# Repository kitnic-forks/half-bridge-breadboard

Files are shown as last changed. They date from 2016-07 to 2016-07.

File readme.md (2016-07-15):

# Purpose #

This is a KiCad project that documents a simple half-bridge circuit, complete with driver.  The
circuit includes room for two TO-220 MOSFETs, two snubber circuits.  It has two logic-level inputs 
which will turn on the upper and lower MOSFETs.

# Details of Operation #

## Power Supply ##

If 10V < V<sub>BATT</sub> < 20V, then the jumper at P2 may be connected so that the
[FAN7842MX](https://www.fairchildsemi.com/datasheets/FA/FAN7842.pdf) is properly supplied.

If V<sub>BATT</sub> < 10V or V<sub>BATT</sub> > 20V, then the user must supply a voltage
between 10V and 20V to the circuit using pin 1 of P1.

## PWM Frequency ##

The circuit is intended to operate as a complete half-bridge using Pulse Width Modulation (PWM) on
the high side AND the low side.  When the upper MOSFET is being operated, it must be operated
synchronously with the lower MOSFET in order to charge the bootstrap capacitor.  The minimum recommended
PWM frequency is 10kHz.

When only the lower MOSFET is being operated, then the upper MOSFET input may be held low while the
lower MOSFET is operated at any frequency desired, including DC.

## Specifications ##

The circuit is intended to operate at a maximum voltage of ~35V and 5A, but these are limitations of
the components and not of the circuit board.  The board - with the proper capacitors and MOSFETs -
should be able to operate as high as 200V at a current of up to 20A.

## Connections ##

### Breadboard ###

If the breatboard power rails are between 10V and 20V and the expected current is under 1A, then P1,
P2, and P3 can be populated on the underside of the board and simply plugged into the breadboard.

When the voltage is outside of the 10V to 20V range, then only pins 1, 2, and 3 of P2 should be
populated and plugged into the breadboard.  The 10V-20V should be supplied to the board through
pin 1 of P1.

### Screw Terminals ###

If P2 is not populated, then power may be supplied through the screw terminals on P4.

# Why Do This? #

I know that there are lots of these sorts of circuits available, but I am continually finding myself
re-drawing this schematic for different circuits.  By placing all of the components for the half-bridge
on one circuit, I have a flexible and extendable starting point for a host of circuits.  Applications
include:

 * DC-DC conversion
 * DC motor drives
 * BLDC motor drives
 
I had a look around and didn't see anything quite like it on Tindie nor a couple of other sites that
I frequent.  World, here ya go.

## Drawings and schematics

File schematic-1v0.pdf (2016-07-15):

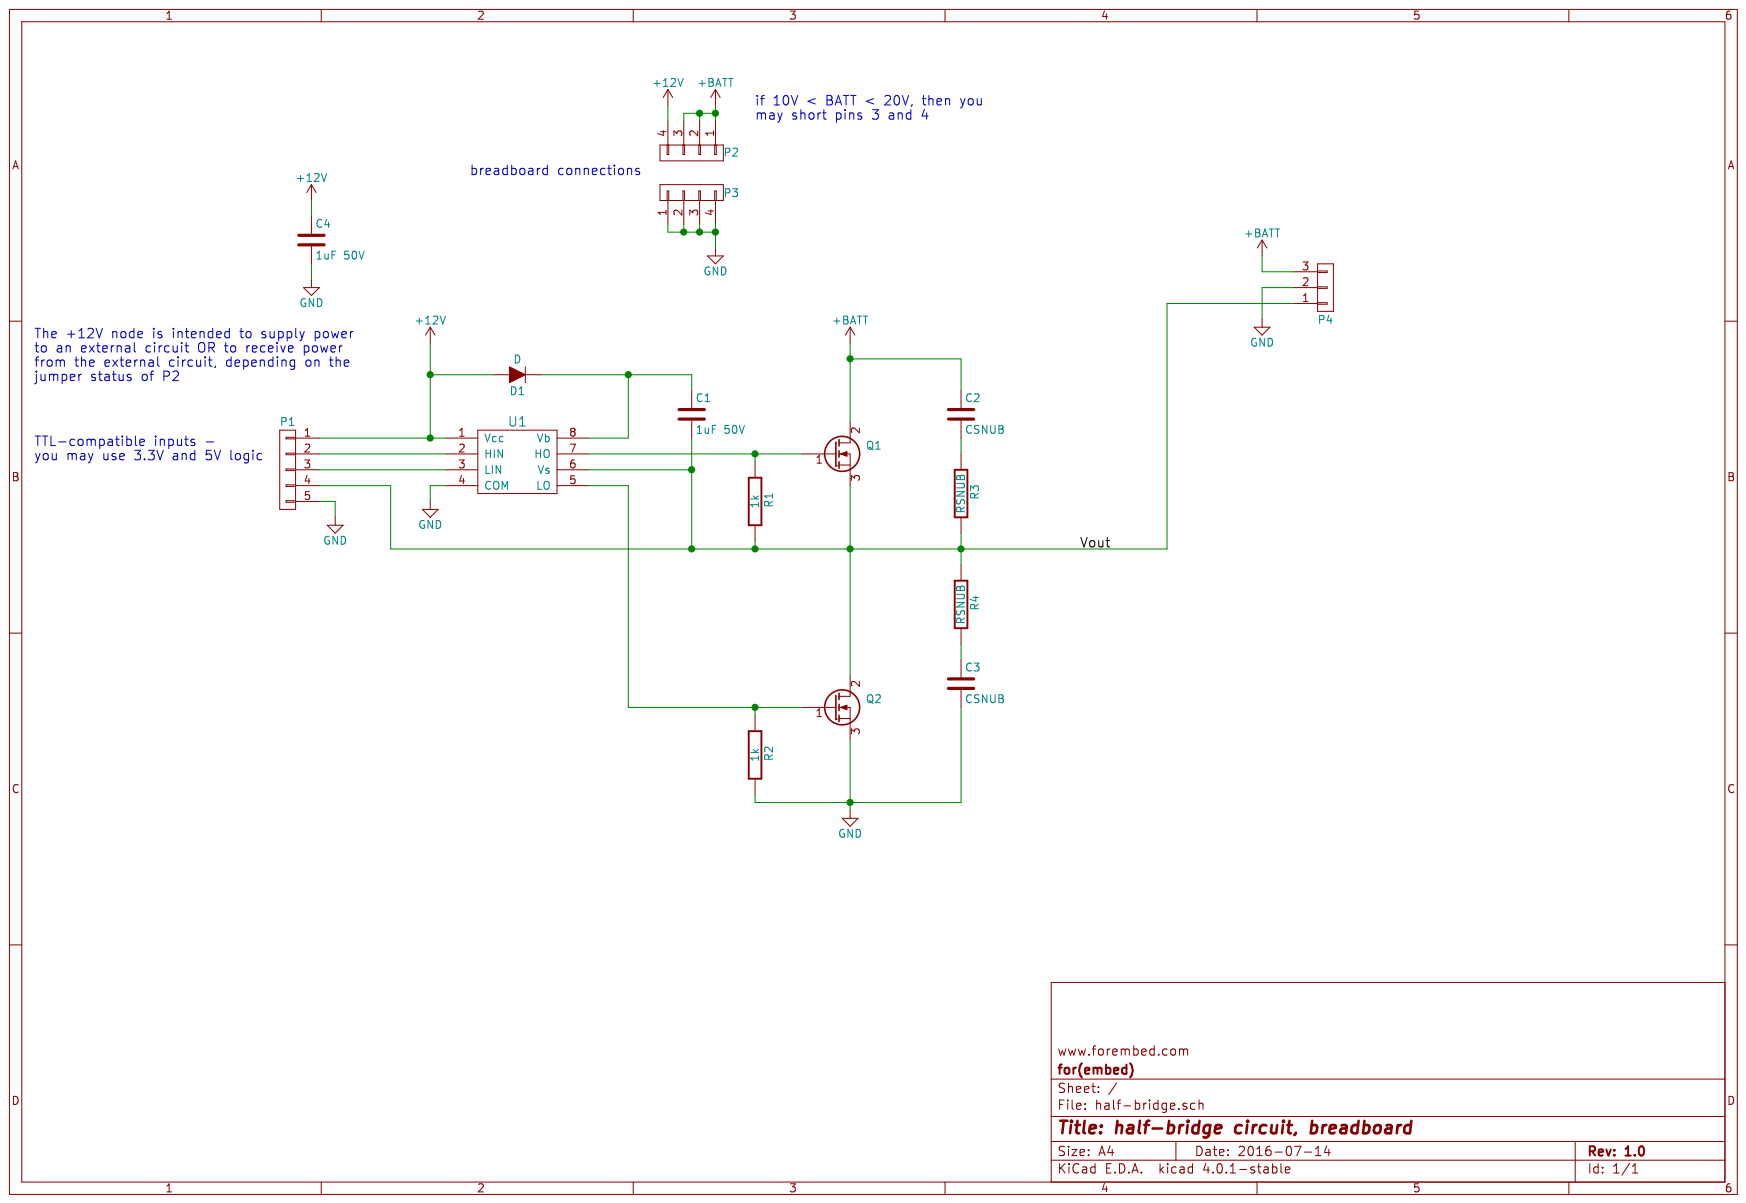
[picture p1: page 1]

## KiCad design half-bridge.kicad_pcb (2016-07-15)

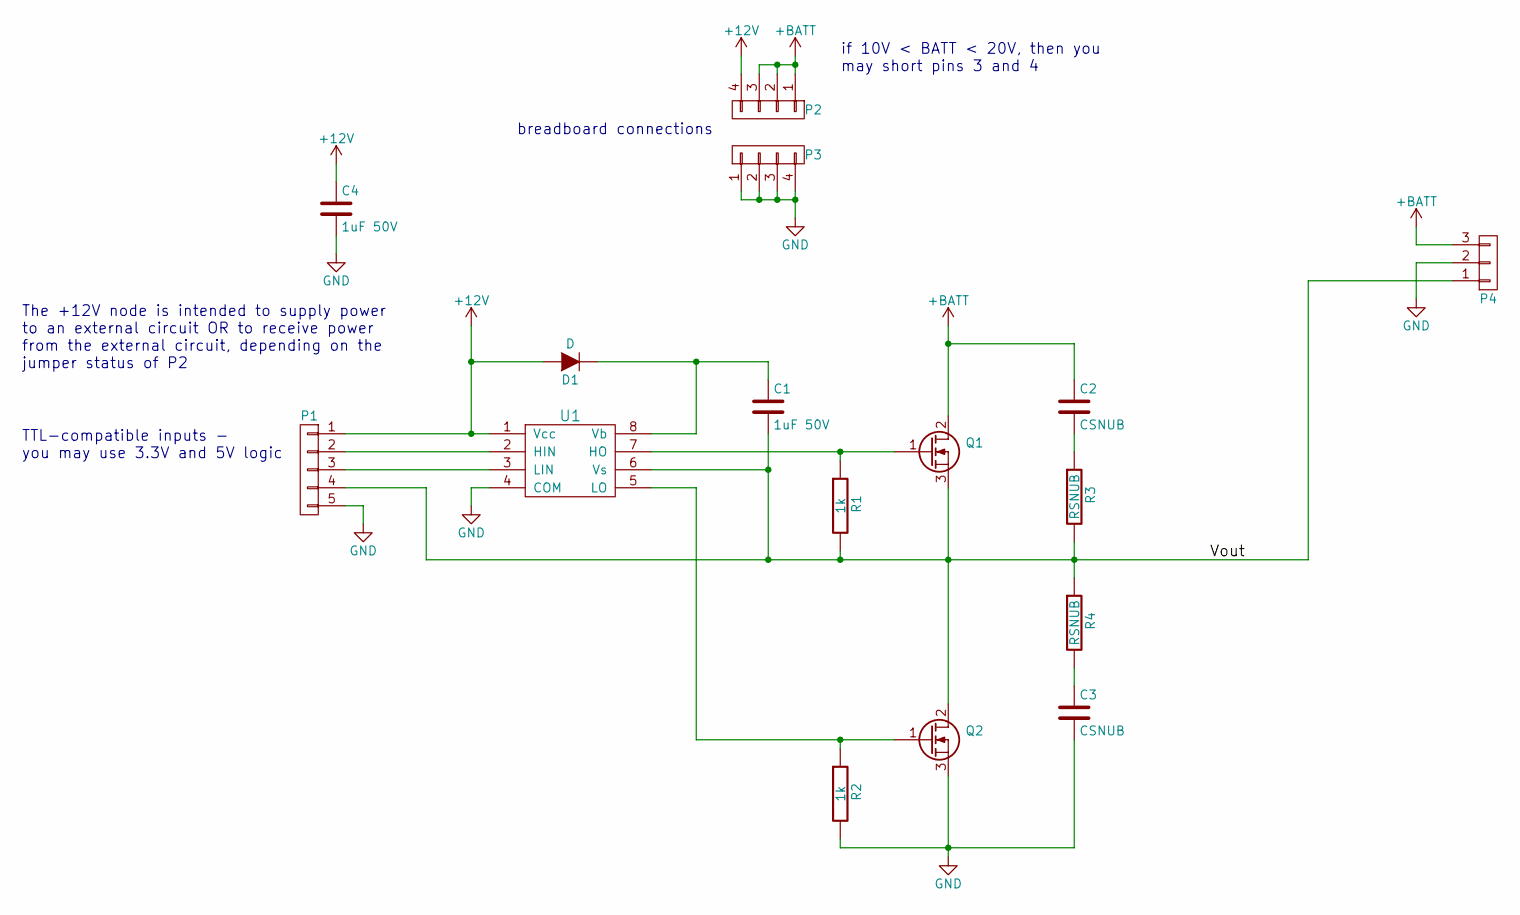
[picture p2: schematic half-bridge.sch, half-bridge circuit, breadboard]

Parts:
C1, C4: 1uF 50V; SM_0805; MPN CL21F105ZBFNNNG
C2, C3: CSNUB; C_Disc_D6_P5
D1: D; SOD-323; MPN 1N914BWS
P1: CONN_01X05; CON_1x5_0.1in
P2, P3: CONN_01X04; CON_1x4_0.1in
P4: CONN_01X03; CONN_1x3_OSTTC032162; MPN OSTTC032162
Q1, Q2: Q_NMOS_GDS; TO-220-VERTICAL; MPN FQP13N06L
R1, R2: 1k; SM_0603; MPN RC0603JR-071KL
R3, R4: RSNUB; Resistor_Horizontal_RM10mm
U1: MOSFET_DRIVER_FAN7842MX; SOIC-8-N; MPN FAN7842MX

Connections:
+12V: C4.1, D1.2 (A), P1.1, P2.4, U1.1 (Vcc)
+BATT: C2.1, P2.1, P2.2, P2.3, P4.3, Q1.2 (D)
/Vout: C1.2, P1.4, P4.1, Q1.3 (S), Q2.2 (D), R1.2, R3.2, R4.1, U1.6 (Vs)
GND: C3.2, C4.2, P1.5, P3.1, P3.2, P3.3, P3.4, P4.2, Q2.3 (S), R2.2, U1.4 (COM)
unnamed: C1.1, D1.1 (K), U1.8 (Vb)
unnamed: C2.2, R3.1
unnamed: C3.1, R4.2
unnamed: P1.2, U1.2 (HIN)
unnamed: P1.3, U1.3 (LIN)
unnamed: Q1.1 (G), R1.1, U1.7 (HO)
unnamed: Q2.1 (G), R2.1, U1.5 (LO)

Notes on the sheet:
if 10V < BATT < 20V, then you may short pins 3 and 4
TTL-compatible inputs - you may use 3.3V and 5V logic
The +12V node is intended to supply power to an external circuit OR to receive power from the external circuit, depending on the jumper status of P2
breadboard connections

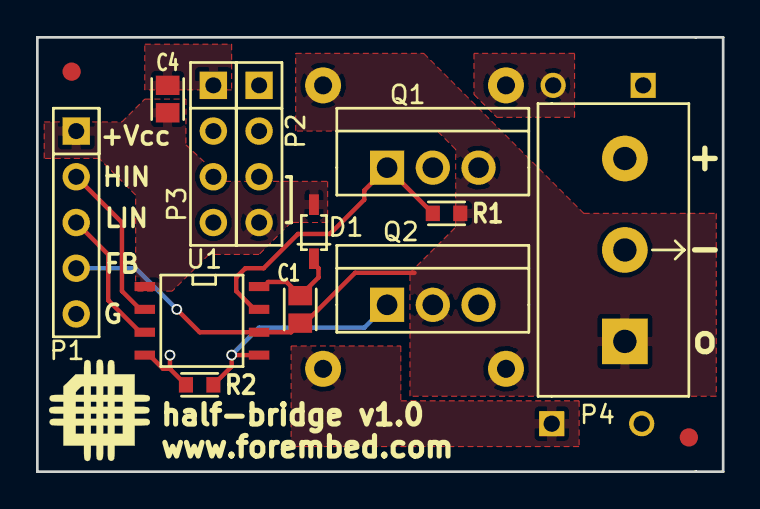
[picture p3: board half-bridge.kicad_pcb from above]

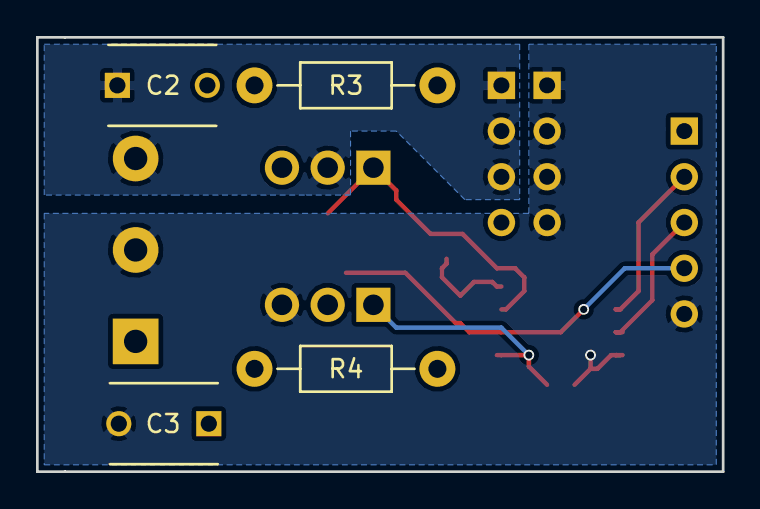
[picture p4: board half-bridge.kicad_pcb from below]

Board: 2 copper layers, 38.1 x 24.1 mm, 18 parts (4 on the bottom side), 11 nets.

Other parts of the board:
FID1, FID1#2: fiducial

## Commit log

2016-07-14 Initial schematic and layout for a half-bridge circuit
    [half-bridge.kicad_pcb, half-bridge.sch]
2016-07-14 Added notes to schematic
    [half-bridge.sch]
2016-07-14 Added PDF version of the schematic
2016-07-14 Updated print settings of the project file
2016-07-15 Added output sense circuit
    [half-bridge.kicad_pcb, half-bridge.sch]
2016-07-15 Added revised schematic
